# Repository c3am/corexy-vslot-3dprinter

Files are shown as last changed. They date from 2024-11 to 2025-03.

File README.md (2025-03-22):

# corexy vslot 3d-printer

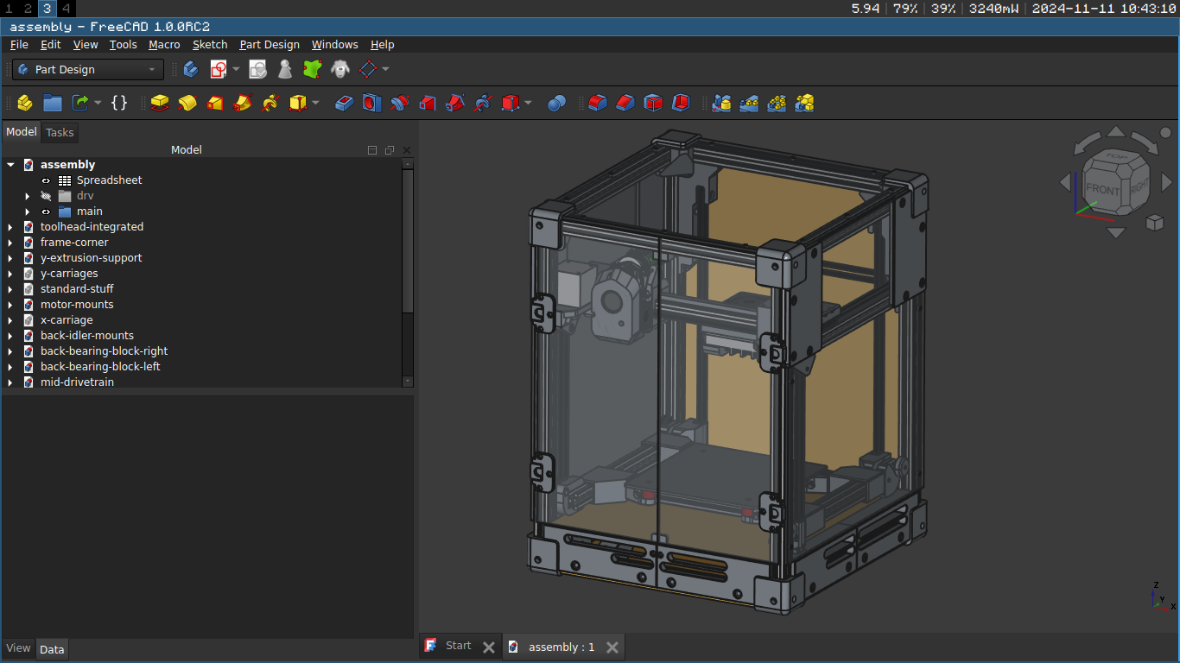
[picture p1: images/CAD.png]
the printer


This printer is not being developed anymore, because I redesigned it from the ground up
to use linear rails instead of v-wheels.
This is the repo for the current version: [current repo](https://github.com/c3am/compact-corexy-3dprinter)

This printer is a cheap enclosed corexy 3d-printer that uses v-wheels.
It has a 180mm cubed print volume and an air exhaust.

## design decisions
- 2020 extrusions
This printer uses 2020 aluminium v-slot extrusions because they are cheap and versitile.
They allow you to mount anything to them easilly with T-nuts and can be solidly
connected to each other using blind joints.

- enclosure
The panels are designed to be lasercut.
The front, side and top enclosure panels are made from 3mm transparent acrylic.
The bottom and back panels are made from 3mm MDF or any other 3mm panel.

- corexy motion system
In a corexy motion system the motors do not move which reduces the moving mass.
This enables higher accelerations as moving mass creates ringing effects which would degrade
the print quality meaning a higher print speed can be achieved.
Also, because there is no moving bed, corexy printers can have a very compact enclosure.

- v-wheels
V-wheels are cheaper than linear rails but might not be as durable/reliable in the long run.

- bed is supported on 4 corners
This ensures that the bed is moving perpendicular to the xy-plane reliably.

- 1 stepper for z
This not only saves on stepper motor costs but also enables the use of mainboards
with only 4 stepper drivers which are cheaper.

- minimal toolhead
because the voron stealthburner toolhead is too big, the mini stealthburner doesn't have
good enough cooling and the dragonburner requires a seperate (expensive) extruder,
This printer has it's own toolhead using BMG extruder gears and a bambulab clone hotend.

- frame corners
Aluminium extrusions can twist when tightening down blind joints which can be prevented
by 3d printed corner pieces which also protect the enclosure panels.
This makes the build easier and improves portability and durability.

- stationary gantry
the xy-gantry is stationary as this is more compact than a flying gantry.

## CAD software
This project uses FreeCAD. All the CAD files are in the CAD folder.
Currently there are no plugins you need to install to open any of the CAD files.
There is one main assembly file where all the parts of the printer are integrated.
You can't just download the assembly.FCStd file because it uses links to integrate all the other
sub-assemblies or parts from the other files. You have to download the whole repository (or the CAD folder)
in order to open the main assembly file.

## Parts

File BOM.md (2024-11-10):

# higher volume material cost
## toolhead
- tz 2.0 hotend kit                 12,00 Eur
- bowden tube                       02,00 Eur
- bondtech extruder gears           05,00 Eur
- 38mm round stepper motor          08,00 Eur

subtotal:                           27,00 Eur

## bed
- 180mm heated bed                  10,00 Eur
- PEI sheet                         10,00 Eur

subtotal:                           20,00 Eur

## motion system
- 3x nema17 stepper motors          18,00 Eur
- 10m gt2 belt                      07,00 Eur
- 1x gt2 16t 5mm pulley             01,00 Eur
- 2x gt2 20t 5mm pulley             02,00 Eur
- 4x gt2 20t 8mm pulley             04,00 Eur
- 2x gt2 32t 8mm pulley             02,00 Eur
- 20t 15mm idler kit                06,00 Eur
- 4x 20t toothed idlers             04,00 Eur
- 8mm stainless steel rods          10,00 Eur
- 13x 24mm v-wheels                 08,00 Eur
- 10x eccentric nuts                02,50 Eur

subtotal:                           64,50 Eur

## frame
- 2020 v-slot extrusions            36,00 Eur
- 20x M6 20mm Linsenkopfschrauben   04,00 Eur

subtotal:                           40,00 Eur

## electronics
- mainboard                         25,00 Eur
- raspberry pi                      25,00 Eur

subtotal:                           50,00 Eur

## mounting hardware

subtotal:                           10,00 Eur

TOTAL:                             211,50 Eur

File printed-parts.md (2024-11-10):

# corexy-vslot-3d-printer printed parts list
## frame (13)
x- x8 corner
x- y-extrusion-support-plate-left-front
x- y-extrusion-support-plate-left-back
x- y-extrusion-support-plate-right-front
x- y-extrusion-support-plate-right-back
x- electronics-mounting-plate

## xy-gantry (13)
x- xy-motor-mount-left
x- xy-motor-mount-right
x- 2x xy-idler-shim
x- y-carriage-left
x- y-carriage-right
### x-carriage
x- x-carriage-front
x- x-carriage-back
x- x-carriage-belt-mount-front-left
x- x-carriage-belt-mount-front-right
x- x-carriage-belt-mount-back-left
x- x-carriage-belt-mount-back-right
x- x-carriage-spacer

## z-motion (12)
### front
x- z-motion-front-idler-mount-left
x- z-motion-front-idler-mount-right
x- z-motion-front-bearing-block-left
x- z-motion-front-bearing-block-right
x- z-motion-endstop-mount

### mid
x- z-motion-mid-motor-mount
x- z-motion-mid-drivetrain
x- z-motion-mid-belt-connector

### back
x- z-motion-back-bearing-block-left
x- z-motion-back-bearing-block-right
x- z-motion-back-idler-mount-left
x- z-motion-back-idler-mount-right

## z-carriage (16)
x- z-carriage-front-left-1
x- z-carriage-front-left-2
x- z-carriage-front-right-1
x- z-carriage-front-right-2
x- z-carriage-back-left
x- z-carriage-back-right
x- z-carriage-belt-mount-1-left
x- z-carriage-belt-mount-1-right
x- z-carriage-belt-mount-2-left
x- z-carriage-belt-mount-2-right
x- z-carriage-extrusion-connection-1
x- z-carriage-extrusion-connection-2
x- z-carriage-extrusion-connection-3
x- z-carriage-extrusion-connection-4
x- z-carriage-bed-mount-1
x- z-carriage-bed-mount-2
x- z-carriage-bed-mount-3
x- z-carriage-bed-mount-4

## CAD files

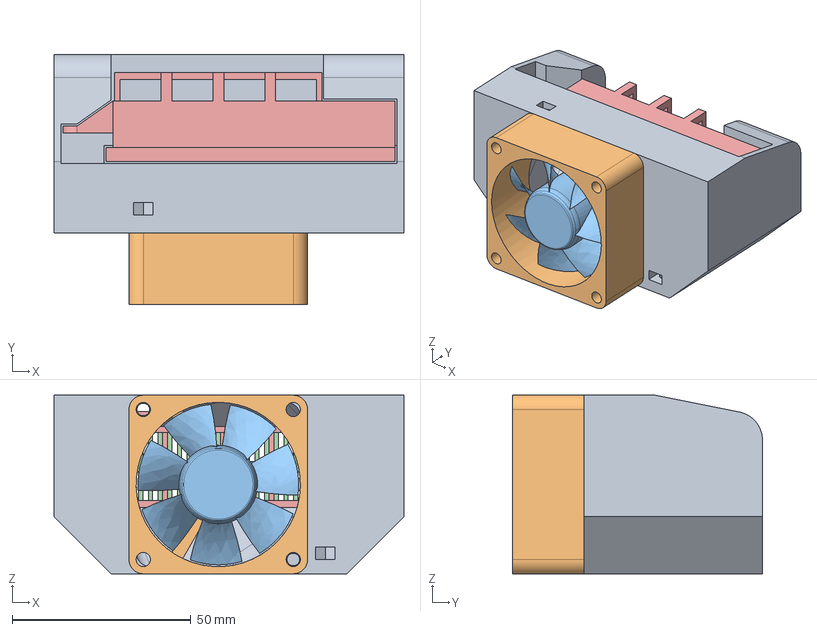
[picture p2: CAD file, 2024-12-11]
CAD/chamber-heater.FCStd
98.0 x 70.0 x 50.0 mm
housing
5020-fan-base-drv
5020-fan-rotor-drv
heater-core-drv
heater-case-drv

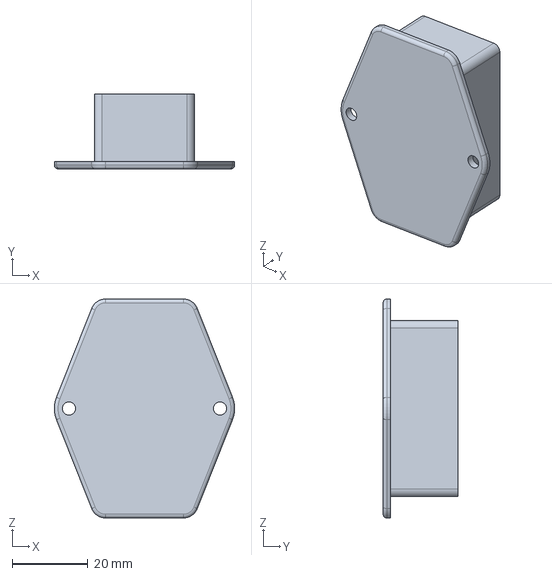
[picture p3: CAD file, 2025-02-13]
CAD/electronics/power-connector.FCStd
47.8 x 19.8 x 58.0 mm

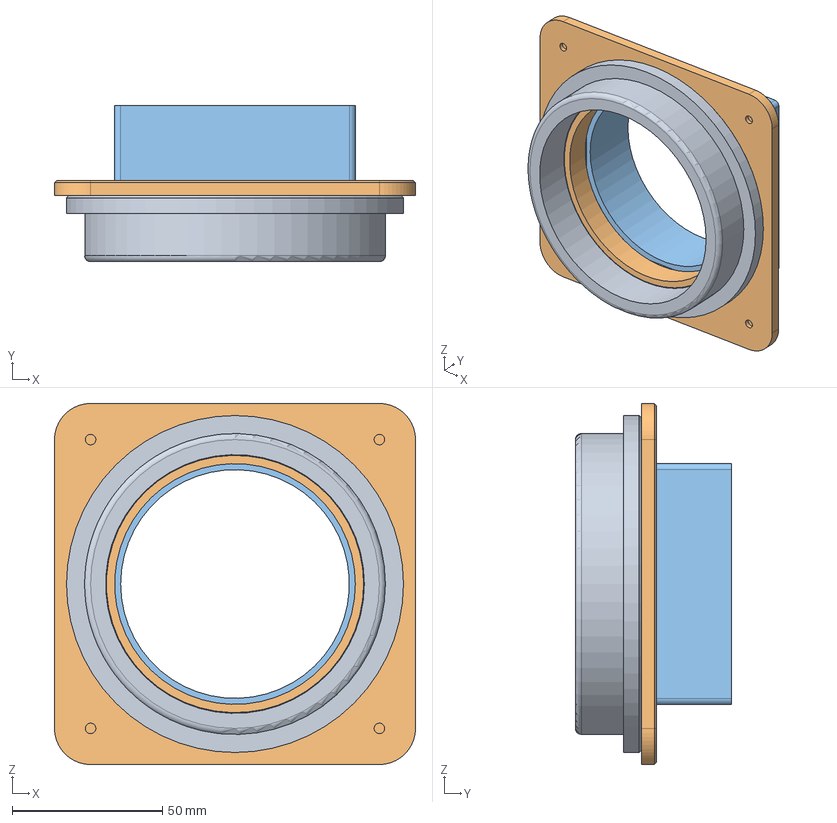
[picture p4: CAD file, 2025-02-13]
CAD/frame/air-exhaust.FCStd
120.0 x 52.0 x 120.0 mm
air-connector-hose
air-connector-chamber
exhaust-fan

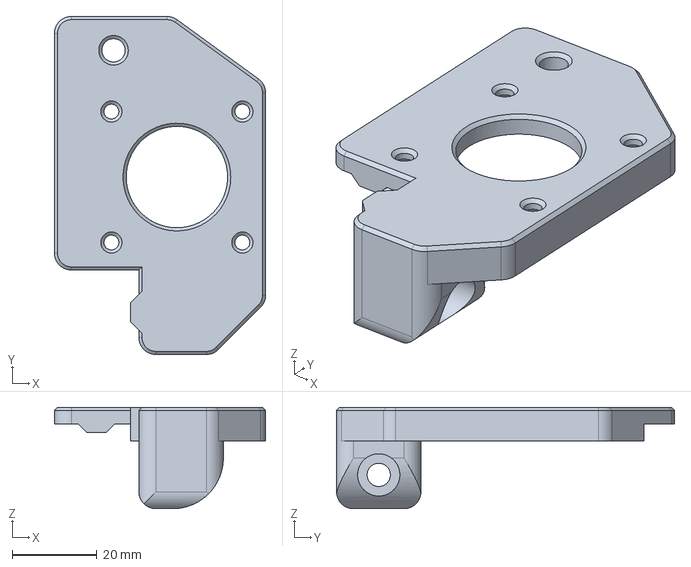
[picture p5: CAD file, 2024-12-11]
CAD/xy-gantry/motor-mounts.FCStd
50.0 x 80.0 x 24.0 mm

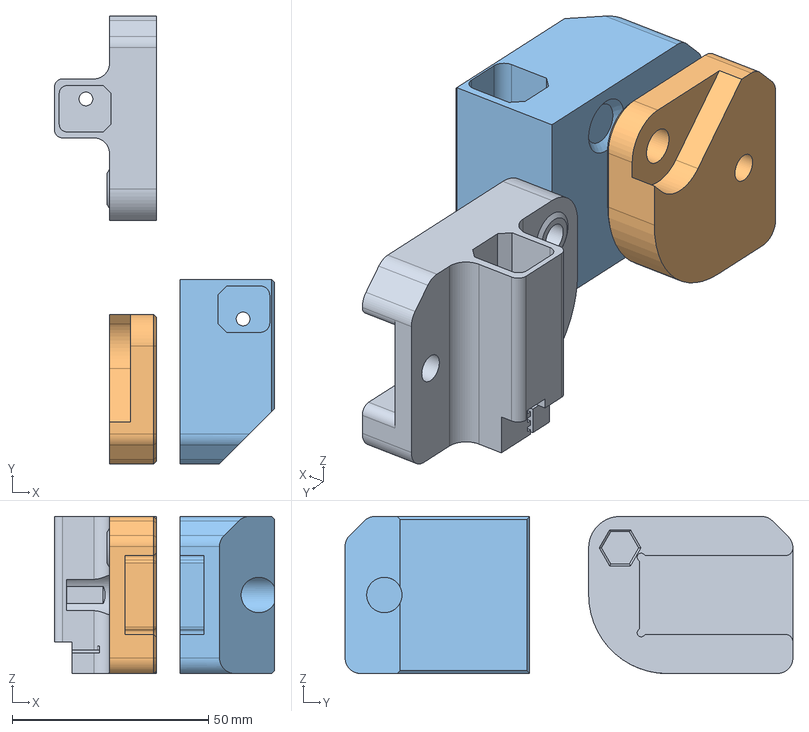
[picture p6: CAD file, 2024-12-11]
CAD/z-carriage/z-carriages.FCStd
56.0 x 114.0 x 40.0 mm
z-carriage-front-left
z-carriage-back-left
z-carriage-belt-mount-left

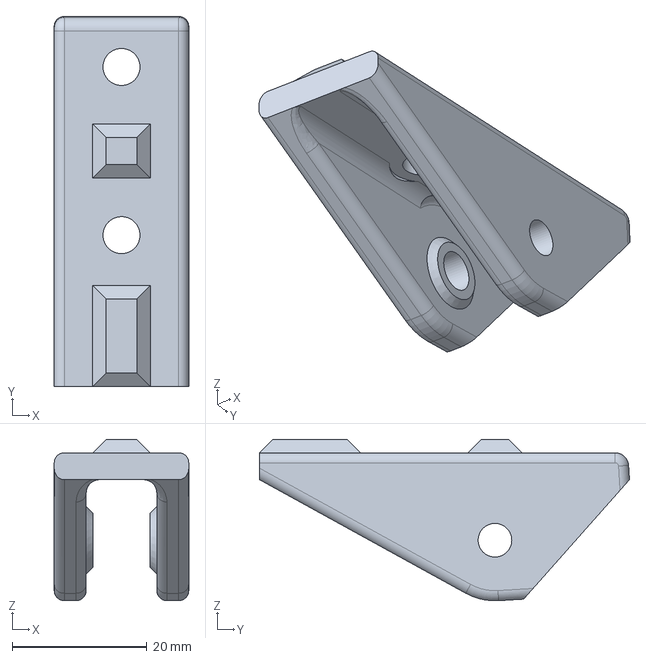
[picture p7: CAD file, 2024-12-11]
CAD/z-motion/front-idler-mount-right.FCStd
20.0 x 55.0 x 24.0 mm

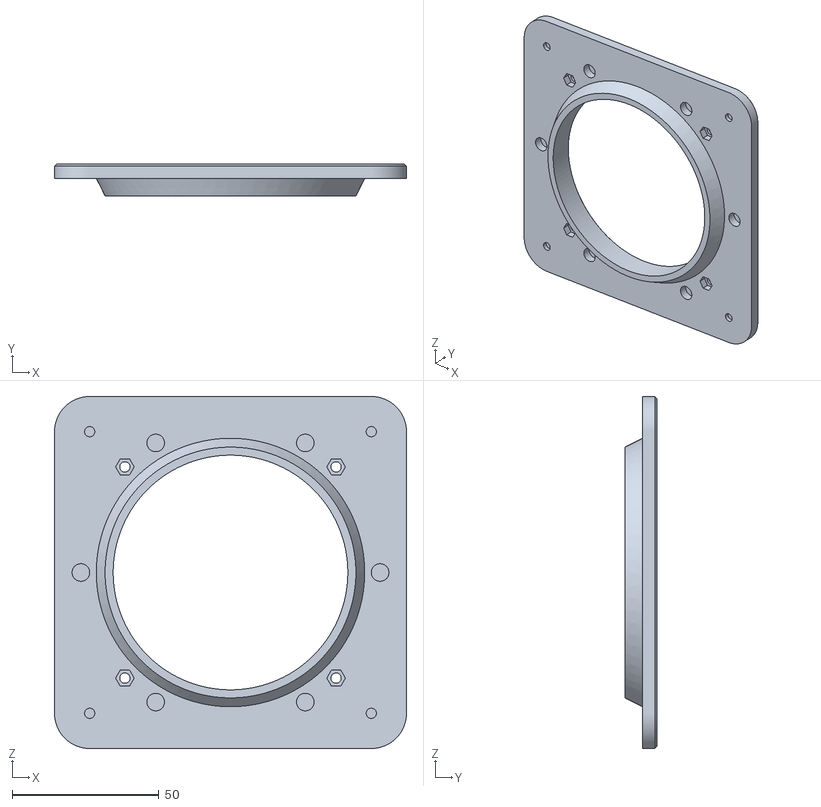
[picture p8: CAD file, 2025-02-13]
stl/air-exhaust-air-connector-chamber.stl
120.0 x 11.0 x 120.0

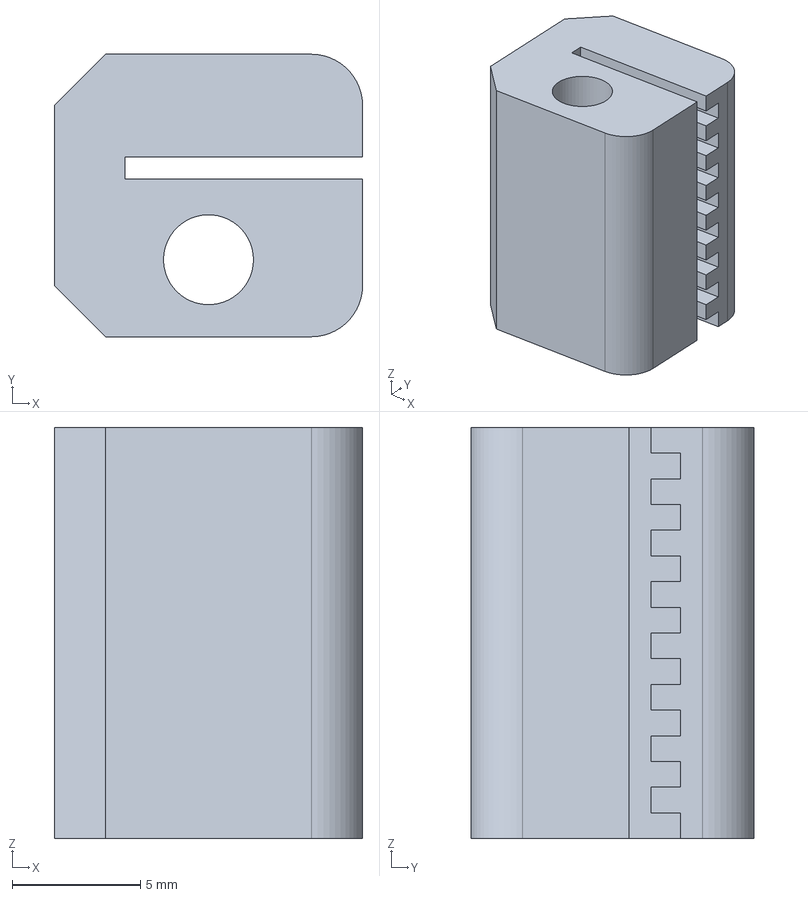
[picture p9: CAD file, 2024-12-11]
CAD/belt-clip.FCStd
12.0 x 11.0 x 16.0 mm

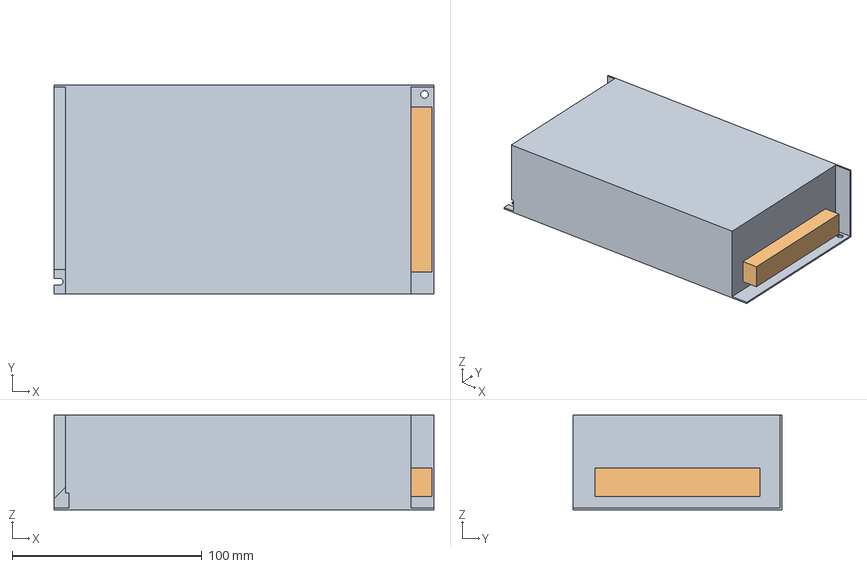
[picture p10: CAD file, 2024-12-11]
CAD/electronics/PSU-12V-10A.FCStd
200.0 x 110.0 x 50.0 mm
terminal-block

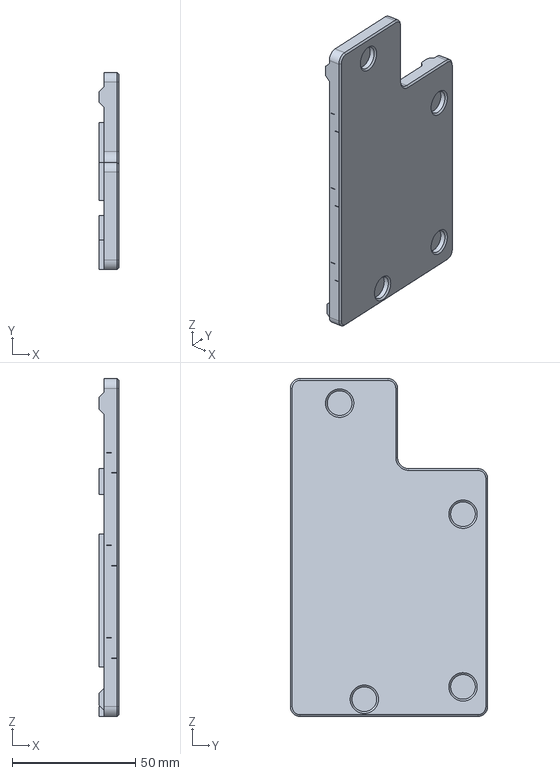
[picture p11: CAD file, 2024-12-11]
CAD/frame/y-extrusion-support.FCStd
8.00 x 80.0 x 137.0 mm

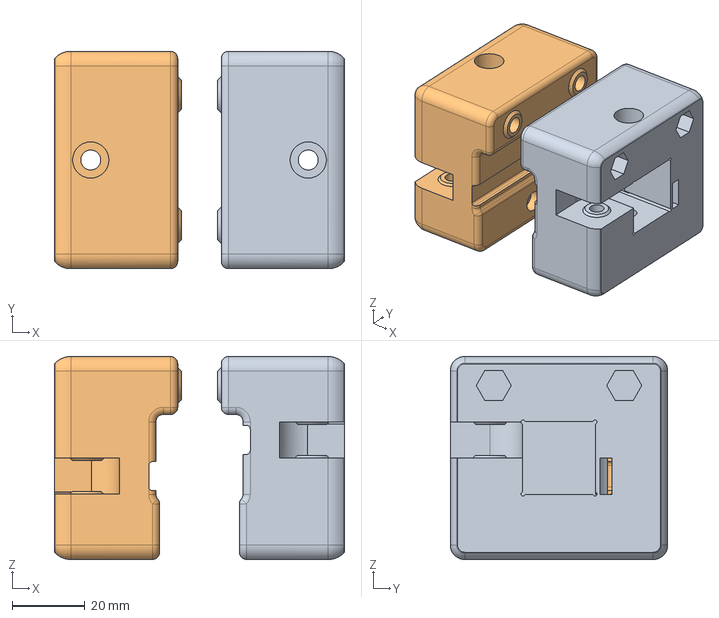
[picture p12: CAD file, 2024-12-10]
CAD/xy-gantry/y-carriages.FCStd
80.0 x 60.0 x 56.0 mm
y-carriage-left
y-carriage-right

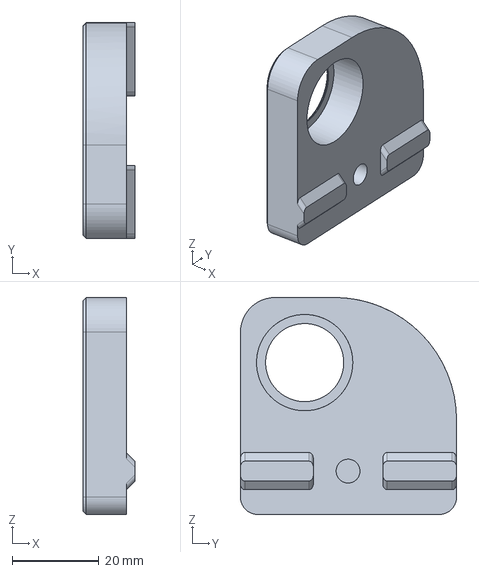
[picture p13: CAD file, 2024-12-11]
CAD/z-motion/front-bearing-block-right.FCStd
12.0 x 49.8 x 50.0 mm

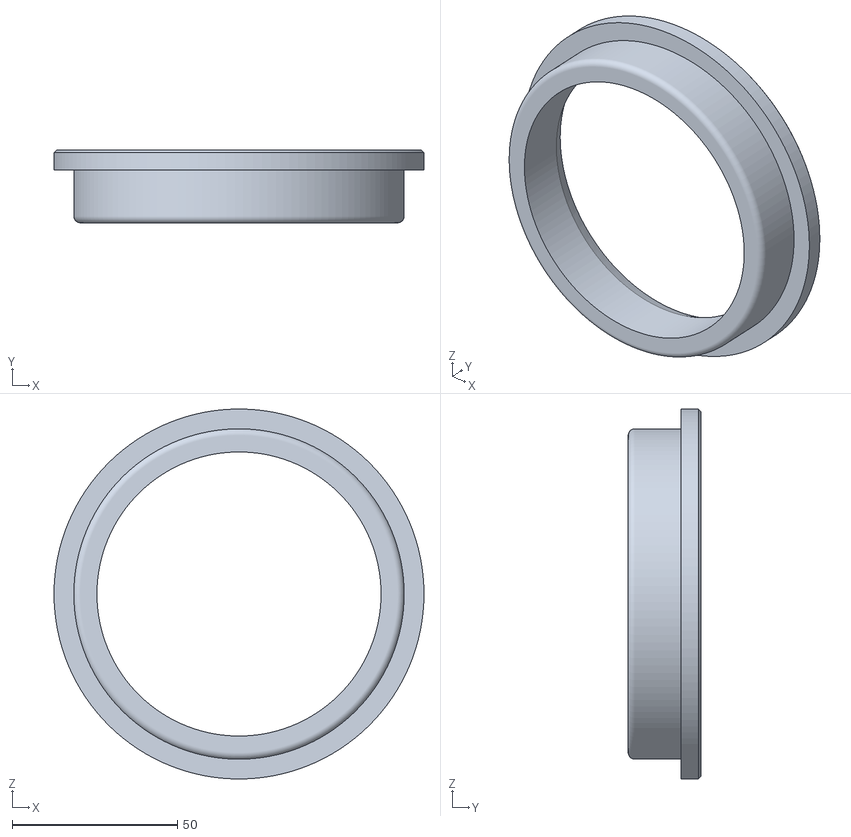
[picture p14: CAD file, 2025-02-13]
stl/air-exhaust-air-connector-hose.stl
112.0 x 22.0 x 112.0

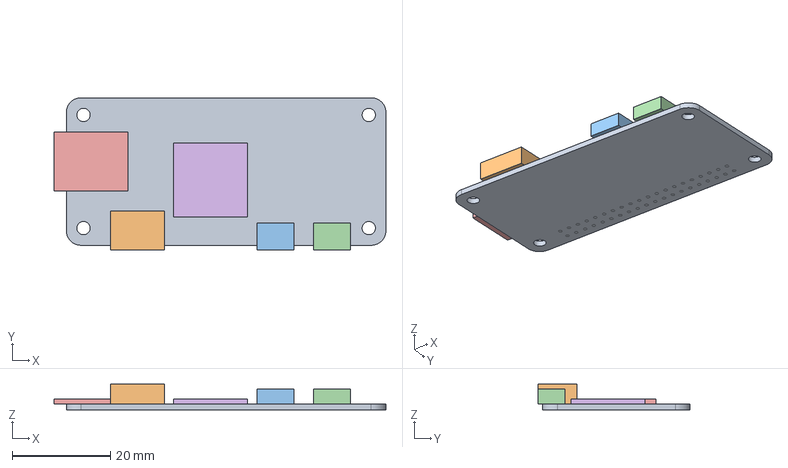
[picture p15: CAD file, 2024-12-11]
CAD/electronics/pi-zero-2-w.FCStd
67.5 x 31.0 x 5.20 mm
PCB
mini-hdmi
usb-power
usb-data
sd-card-slot
cpu

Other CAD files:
panels/dxf/back.dxf
CAD/frame/intake-vents.FCStd
CAD/simple-bmg-extruder.FCStd
CAD/z-motion/back-bearing-block-left.FCStd
CAD/electronics/bigtreetech-mini-e3-v2.0.FCStd
CAD/frame/frame-corner.FCStd
CAD/standard-stuff.FCStd
CAD/wire-mount-frame.FCStd
CAD/xy-gantry/x-carriage-old.FCStd
CAD/z-motion/back-bearing-block-right.FCStd
CAD/z-motion/back-idler-mounts.FCStd
CAD/z-motion/mid-drivetrain.FCStd

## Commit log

2024-06-14 increased frame height and cleaned things up
2024-06-14 rear-idler-mounts improved
2024-11-10 pretty much everything changed LOL
    [assembly-frameClone009.stl, back-bearing-block-left.FCStd, back-bearing-block-right.FCStd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]
2024-11-11 fixed directory of CAD image
2024-11-11 added instructions for opening/editing cad files
    [tz-2.0.step]
2024-11-16 fixed clearances in the extruder
2024-11-17 removed washer spacing from drivetrain and motor-mounts
    [assembly-frameClone009.stl, back-bearing-block-left-z-motion-back-bearing-block-leftz-motion-back-bearing-block-left.stl, back-bearing-block-right-z-motion-bac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]
2024-11-17 made all motor mounting scres countersunk m3 8mm
    [motor-mounts.FCStd]
2024-11-17 added motor cable connector clearance in mid-drivetrain
    [assembly-z-carriagebed-extrusion-connection-back-left.stl, assembly-z-carriagebed-extrusion-connection-front-left.stl, mid-drivetrain.FCStd]
2024-11-17 rounded corner off on z-motion-front-bearing-block-mid
    [assembly-z-motion-bearing-block-mid.stl, mid-drivetrain.FCStd]
2024-11-17 adjusted clearances in the z-carriage extrusion connection parts
2024-11-18 simplified z-motion-front bearing-block mid
    [assembly-z-carriagebed-mount-1.stl, assembly-z-motion-bearing-block-mid.stl, x-carriage-xy-gantryx-carriage-back.stl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]
2024-11-23 exported svg files for lasercut panels
    [back-bearing-block-left.FCStd, back-bearing-block-right.FCStd, back-idler-mounts.FCStd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]
2024-11-26 some changes ...
    [belt-clip.FCStd, z-carriages.FCStd]
2024-11-28 fixed door hinge clearances
    [assembly-framelower-door-stopper.stl, assembly-frameskirt-back-left.stl, assembly-frameskirt-back-right.stl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]
2024-12-01 added electronics mounting plate
    [PSU-12V-10A.FCStd, assembly-electronics-mounting-plate.stl, assembly-framelower-door-stopper.stl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]
2024-12-10 added power port and bed cable hole
    [assembly-frameskirt-right-back.stl, assembly-hinge-stat-drv.stl, front-idler-mount-right.FCStd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]
2024-12-11 added air exhaust fan and intake vents
    [PSU-12V-10A.FCStd, air-hose-connector.FCStd, back-bearing-block-left.FCStd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]
2025-02-13 updated README to point to current repo
    [PSU-12V-10A.FCStd, air-exhaust-air-connector-chamber.stl, air-exhaust-air-connector-hose.stl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]
2025-03-22 fixed link to current repo
